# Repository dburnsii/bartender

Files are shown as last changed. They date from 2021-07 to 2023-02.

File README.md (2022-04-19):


# The Bartender

Product Video (https://youtu.be/YWqvJ5PAxSI)

The Bartender is an intelligent, robotic, drink-making machine. It's made to
display your bottles and pour you a cocktail just the way you like. The scale
ensures your ingredients are measured precisely, and the touchscreen interface
makes it easy to use. Each led in the light strip above the bottle deck can be
controlled individually, meaning they can highlight an empty bottle for you,
or they can put on a gentle light show to provide ambiance to a room. All told,
the Bartender is the perfect addition to any bar setup to make it quick, easy,
and fun to enjoy a casual drink, or to keep your guests glasses full.

## Contents
 - [About the Project](#About-the-Project)
 - [Getting Started](#Getting-Started)
 - [Hardware](#Hardware)
 - [Software](#Software)
 - [Contributing](#Contributing)
 - [Roadmap](#Roadmap)
 - [Contacts](#Contacts)

### About the Project
**The Bartender**'s design is made to integrate into a room first, and to easily
pour drinks second. The problem with many drink making machines is the need for
dedicated table space, which makes it feel like an appliance rather than a part
of your setup. With two drawers for storage, and knobs or handles on the front
side, **The Bartender** feels like a cabinet with some extra wizardry, and can
also hold things like Margarita Salt or tools like a stirrer.

[Demo Video](https://youtu.be/VJUhfgaUki0)

### Getting Started
The Bartender calls for equal parts hardware and software, so some woodworking
and soldering is required. Currently you'll have to buy the components and
assemble yourself, but if the project gains popularity, kits may become available.

### Hardware
As mentioned above, you'll need to do some woodworking to get the drinks
flowing. The cut list is available in the `hardware` directory, and the BOM
is available there as well. After purchasing and assembling the required
hardware, you can move on to getting the Raspberry Pi set up.

### Software
#### Build Requirements
 - [**Qemu User Static**](https://github.com/multiarch/qemu-user-static) - Multi-platform build support
  - [**Docker**](https://www.docker.com/) - Build environment

#### Development
- [**Kicad**](https://www.kicad.org/) - PCBs
- [**FreeCad**](https://www.freecadweb.org/) - 3D Models
- [**Platform.io**](https://platformio.org/) - For Arduino Companion

#### Runtime
 - [**Raspberry Pi OS**](https://www.raspberrypi.org/software/) - Operating System
 - [**React**](https://reactjs.org/) - Frontend
 - [**Python**](https://www.python.org/) - Backend Microservices

#### Installation
 1. Install [Raspberry Pi OS](https://www.raspberrypi.org/software/) on your Pi
 2. Add **The Bartender**'s official Debian repo to your `/etc/apt/sources.list` file:
   - `echo "deb https://storage.googleapis.com/bartender-repo bullseye main" | sudo tee -a /etc/apt/sources.list`
 3. Add **The Batender**'s secure GPG key for updates:
   - `wget -O - https://storage.googleapis.com/bartender-repo/bartender-repo.gpg.key | sudo apt-key add -`
 5. Reboot and grab a glass!

#### Updating
  Navigate to the "Settings" screen, and press "Upgrade". Reboot.

  The upgrade function is a very new feature, and may experience some problems.
  To troubleshoot, please file an issue here and run
  `sudo apt-get update && sudo apt-get -y upgrade` manually to get your system
  up to date.

### Contributing
This project is still in the early phases and the repo is subject
to changes and reorganization. Feel free to make suggestions and
submit a pull request for any desired features.

### Roadmap
The end goal for this project is to provide assembled units for anyone to use,
but getting there is a huge undertaking. With the help of contributors,
**The Bartender** can get there, but even if it doesn't, it's a fun project
to play with, and a great way to learn many different skills.

### License

See [LICENSE](LICENSE)

### Contacts
Desone Burns II - dburnsii@live.com - https://desone.dev

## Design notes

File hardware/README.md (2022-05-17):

# Hardware

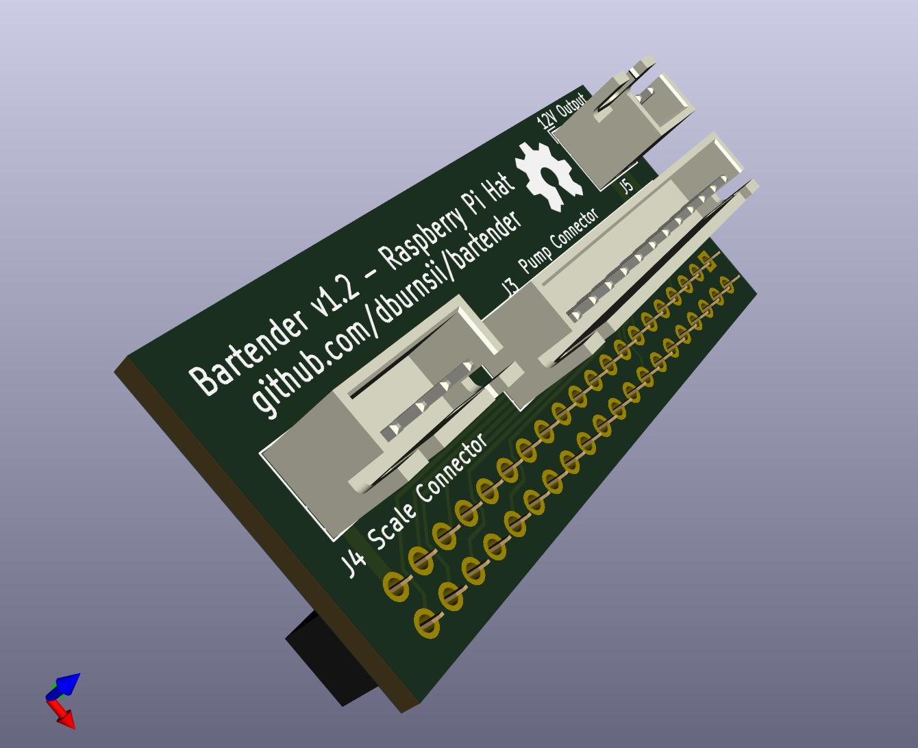
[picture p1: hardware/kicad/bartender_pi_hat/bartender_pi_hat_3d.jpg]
Pi Hat PCB


Here you'll find all the hardware you'll need to assemble your own **The Bartender**.
There are quite a few parts you'll need, and most of them can be purchased for very
cheap from eBay, however you'll likely end up with more parts than you'll need for
most things. As this project gains popularity, kits may become available to make
getting started a lot easier.

## Part List
The parts in the parts list were sourced due to their high availability. **The
Bartender** is a relatively advanced system, but it's made up of components that
are easy to get a hold of.

## Cut List

The list of cuts you'll need to make to the single 4'x8' sheet of plywood are
available in .csv format. My current favorite tool for this purpose is
[CutListOptimizer](https://www.cutlistoptimizer.com/). It isn't a FOSS tool,
but you should only need to use it once or twice, optimizing for the blade
you're using to cut the wood. The full 3D model of the bartender is available in
FreeCAD, with assembly instructions to come.

## Roadmap

The intention for this project is to combine and optimize these components
both for bringing down the price, and for ease of accessibility. I personally
(@dburnsii) am not a hardware engineer nor do I have a background in Hardware,
so I recognize that there is a lot of room for improvement in optimizing the
PCBs, cleaning up and optimizing the frame build, etc. My hope is that the
open-source community will band together and make this the drink-making robot
of the future!

### Milestones

#### Single Board Setup
**The Bartender** should have all connections come from the same PCB, rather than
using separate power supplies and a separate pump array board.

 - [ ] Run all 5v components from a 12v -> 5v buck converter (or other step-down)
 - [x] Run Neopixels (accent lighting above bottles) directly from the Pi
 - [ ] Affix the Pump-Controller board components to the Pi Hat

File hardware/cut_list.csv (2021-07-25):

Length | Width | Qty | Label | Enabled
48 | 24 | 1 | Frame Back | true
48 | 6 | 2 | Frame Top & Bottom | true
23 | 6 | 2 | Frame Left & Right | true
47 | 6 | 2 | Frame Shelves | true
6 | 4 | 2 | Drawer Barrier | true
16 | 4 | 2 | Drawer Faces | true
5 | 3.5 | 4 | Drawer Sides | true
15 | 3.5 | 2 | Drawer Rear | true
14 | 5 | 2 | Drawer Bottom | true
47 | 5.5 | 1 | Pump Door | true

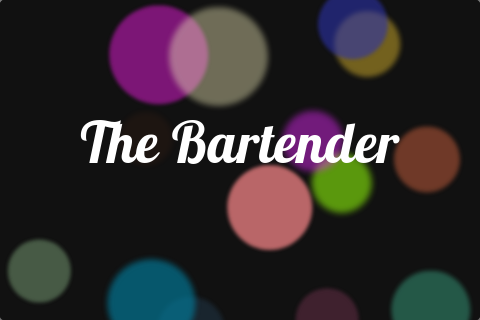
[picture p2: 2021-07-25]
screensaver.png

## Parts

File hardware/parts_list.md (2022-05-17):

# Parts List
Below is the list of parts that you'll need in order to build your own The Bartender!

### Custom PCBS
The Bartender has a few PCBs that make assembly and maintenance a lot easier:
 - [ ] [Pump Array](https://oshpark.com/shared_projects/H87zFAoN) - $26.80 (for 3, $8.93 each)
 - [ ] [Raspberry Pi Hat](https://oshpark.com/shared_projects/1Qw7b2lh) - $9.80 (for 3, $3.27 each)

 Total: $36.60 ($12.20 for a single set)

 All Prices are as listed from OshPark, and each order includes a minimum of 3 boards. The CAD files for these boards are provided, and you may be able to find them cheaper elsewhere.

### For the PCBs

#### Pump Array
 - [ ] 10x TIP-120 (~$6/10pcs)
 - [ ] 10x 1N4001 Diodes (~$3/10pcs)
 - [ ] 10x 1k Resistors (~$3/10pcs)
 - [ ] 11x 2-pin JST-XH Headers (~$5/50sets (includes cables))
 - [ ] 10x 2-pin JST-XH Cables (various lengths, for the pumps)
 - [ ] 1x 12-pin JST-XH Header ($5/20pcs)
 - [ ] 1x 12-pin JST-XH 20cm Cable ($9/5pcs)

#### Raspberry Pi Hat
 - [ ] 1x 12-pin JST-XH Connector (included above)
 - [ ] 1x 4-pin JST-XH Right-Angle Connector (~$5/10 sets)
 - [ ] 1x 3-pin JST-XH Connector (~$5/50sets)
 - [ ] 1x 2-pin JST-XH Connector (Optional, included above)
 - [ ] 1x 2x20-pin Female Header (~$2)

#### HX711 Module
 - [ ] 2x 4-Pin JST-XH Right-Angle Connector (included above)
 - [ ] 1x 10KG Load Cell (Often included with HX711 module)

Total: ~$43

### Off-The-Shelf
 - [ ] 1x Raspberry Pi 4 2GB ($35)
 - [ ] 1x 8GB MicroSD Card ($6)
 - [ ] 1x Waveshare 5" DSI Touchscreen ($45)
 - [ ] 1x HX711 Module (Shielded) ($2)
 - [ ] 1x 2M Addressable LED Strip ($15)
 - [ ] 1x 12v 1A Power Supply ($6)
 - [ ] 1x 5v 5A Power Supply (USB-C) ($7)
 - [ ] 1x Fused AC Inlet ($3)
 - [ ] 10x 365 DC Pump ($8)
 - [ ] 1x 1KG Roll of 3D Filament (Any Color) ($15)

Total: ~$142

### The Home Depot
 - [ ] 1x 4'x8'x1/2" Sheet MDF (~$37.00)
 - [ ] 2x Box Wood Screws (3/4" and 2") (~$5 + $10)
 - [ ] 3x Drawer Handles (~$5)
 - [ ] 4x Inset Cabinet Hinges ($8/pair)
 - [ ] 4x Double Roller Catch for Cabinet (~$1)
 - [ ] TBDx M4 Screws and nuts (~$10)
 - [ ] 1x 5m 1/4" ID 3/8" OD Vinyl Tubing (~$10)
 - [ ] 1x 1m 3/8" ID 1/2" OD Vinyl Tubing (~$4)

Total: ~$101

### Tools
 - [ ] Circular or Table Saw
 - [ ] Soldering Iron
 - [ ] Drill
 - [ ] Spade Drill Bit Set

Grand Total: ~$298.20

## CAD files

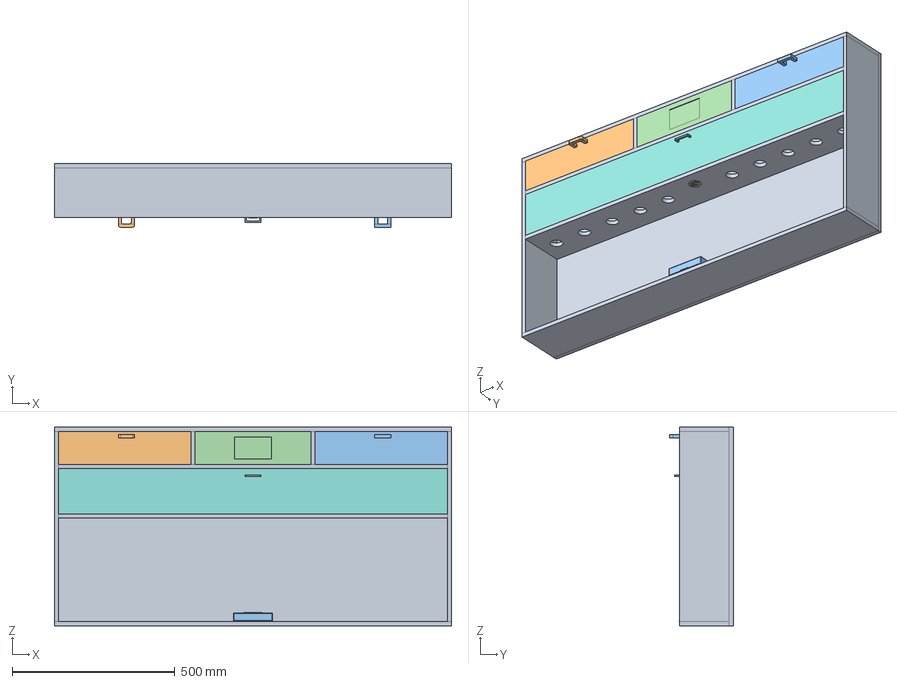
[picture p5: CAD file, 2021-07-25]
hardware/freecad/BartenderAssembly.FCStd
1219.2 x 195.1 x 609.6 mm
FullFrame
SpoutGuide
ScaleBody
ScalePlate
ScaleBracket
LoadCell
ScaleBaseTray
PumpDoor
LCD
SpareDrawerLeft
SpareDrawerRight
LCD Holder

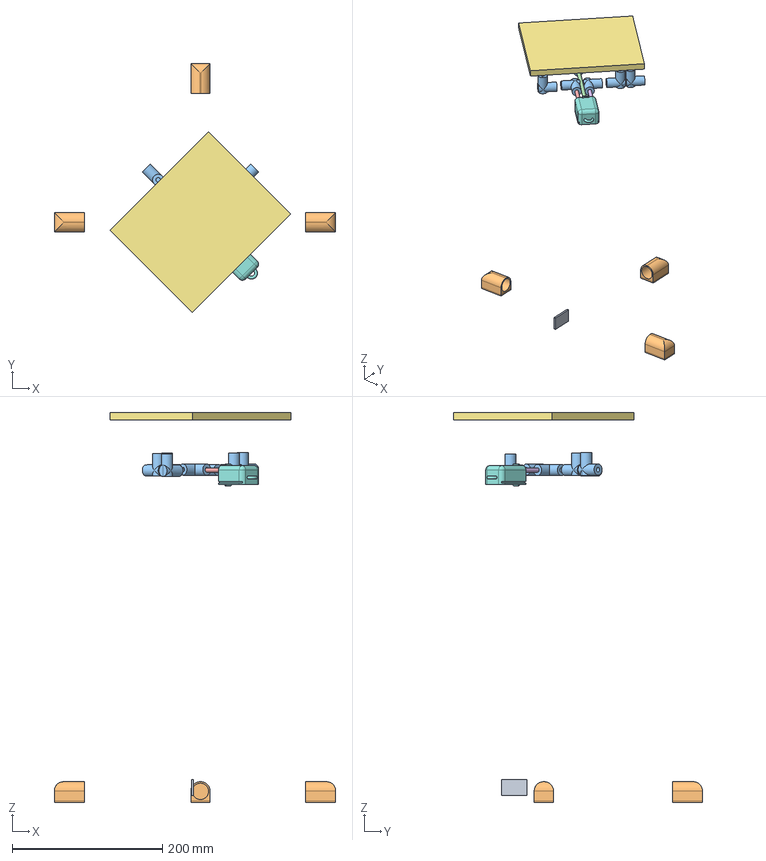
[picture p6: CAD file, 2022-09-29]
hardware/freecad/Mini/BartenderMini.FCStd
374.5 x 331.2 x 518.9 mm
ScalePCB
Foot South x 3
Tubing Elbow 001 x 7
Tubing 001
Tubing 002
Tubing 003
Lid
Spout

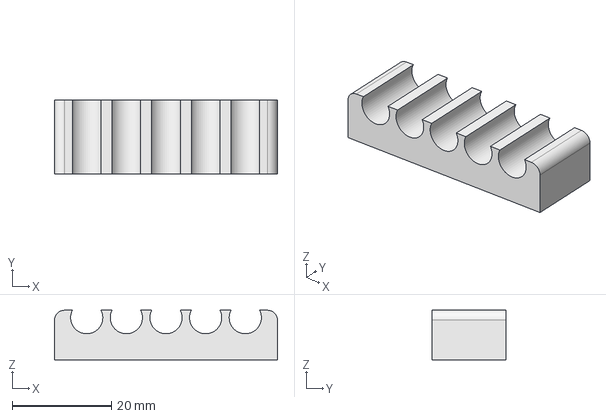
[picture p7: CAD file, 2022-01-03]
hardware/freecad/TubingGuide.FCStd
45.0 x 15.0 x 10.0 mm

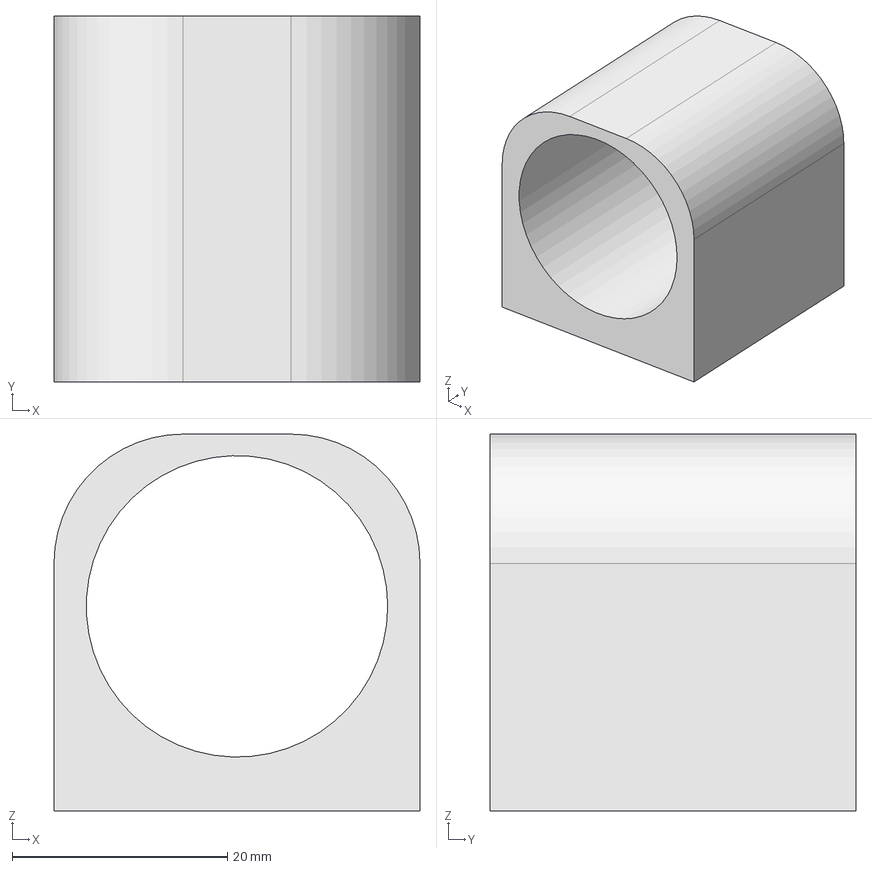
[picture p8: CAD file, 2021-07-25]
hardware/freecad/PumpHolder.FCStd
34.0 x 34.0 x 35.0 mm

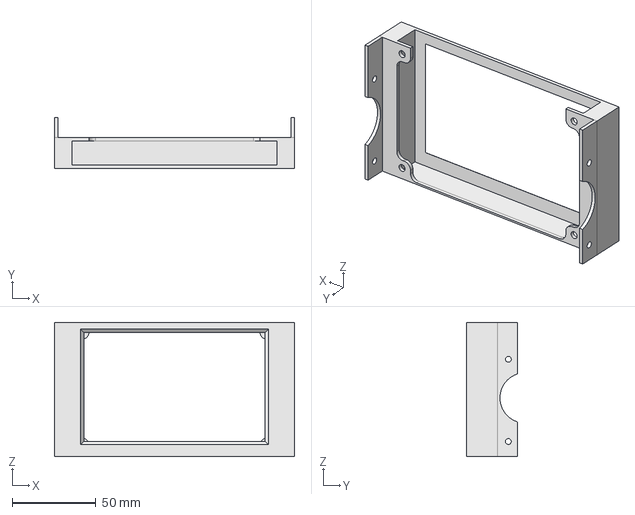
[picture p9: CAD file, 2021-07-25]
hardware/freecad/ScreenMountv2.FCStd
143.0 x 30.5 x 80.0 mm

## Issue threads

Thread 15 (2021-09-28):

Add manual pour mode

dburnsii, 2021-09-28:

dburnsii, 2021-09-28:
Certain ingredients are currently not compatible with the bartender (i.e. carbonated liquids). There should be a way to pour these ingredients into the glass manually, using the LEDs to indicate to the user how much to pour (still utilizing the scale).

Closed 2022-01-03.

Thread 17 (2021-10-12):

Add calibration configuration

dburnsii, 2021-10-12:
HX711 modules tend to be subject to some temperature drift as well as some sensitivity drift. Add a page to the interface to calibrate with a known amount of liquid or weight.

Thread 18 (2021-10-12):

Add upgrade button

dburnsii, 2021-10-12:
Now that the database is transferred to sqlalchemy and migrations are possible, create an `upgrade.sh` script to check for system upgrades (currently via the git repo), to be launched by the system service. Subsequently rebuild the frontend and run any migrations, then reboot.

Closed 2022-04-13.

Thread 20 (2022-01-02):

Add cleaning mode

dburnsii, 2022-01-02:
One of the menus available should be a cleaning mode. The pumps should add in "last loaded" and "last cleaned" columns to the database, for letting users know in the future when they should clean a pump. The cleaning mode should be simple: activate it for a given pump with the water loaded, run some amount of water through (maybe a couple cleaning mode levels), and do some pulses to free anything that may be stuck.

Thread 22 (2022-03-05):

Eliminate the companion chip

dburnsii, 2022-03-05:
LED strip should be driven directly by RPi

dburnsii, 2022-03-10:
Driving the LED strip directly from the RPi has been validated, but will require some rework to the led_server, as well as an update to the PCB HAT.

dburnsii, 2022-03-10:
Depends on #29

Closed 2022-09-25.

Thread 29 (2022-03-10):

Integrate Motor driver and HAT

dburnsii, 2022-03-10:
The motors for the bartender can be driven by an SMD transistor. Rework the PCB to integrate the motor driver to use SMD components, and also include a port for the LED strip in the rework.

Closed 2023-01-15.

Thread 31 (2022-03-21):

Firefox over Chromium or other browsers

dburnsii, 2022-03-21:
This issue is just for record keeping purposes.

The motivation for choosing Firefox over Chromium for this project is that Chromium supports a minimum browser height of 500 pixels, where the screen in use is only 480. The html element could be modified to account for this, but leads to a bunch of exceptions in the case to make it work, which will make it harder to get this working on external devices (phone browsers for instance)

Closed 2022-03-21.

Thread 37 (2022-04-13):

Rework manual pour screen

dburnsii, 2022-04-13:
Instead of cramming all of the bottle actions into a small space, perhaps make the manual pour screen more of a menu, where the user selects the desired bottle, and then a modal pops up with more options. This modal could have more than just a pour button, it could also have options for measured pours.

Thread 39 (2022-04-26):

Reduce SD Card Writes

dburnsii, 2022-04-26:
By default, Raspberry Pi OS does lots of reads and writes to the SD card. Since the lifespan of these cards is relatively short, add settings to reduce the number of reads and writes as much as possible.

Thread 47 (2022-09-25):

Convert LEDs to I2C

dburnsii, 2022-09-25:
With looking at multiple boards, and considering some of the issues seen with custom protocols regarding timing, all devices that communicate with the main board should be communicating with I2C.

For the LEDs, this will likely mean creating a custom firmware on an MCU, likely an Arduino. This will differ from the old design in that it will use protocol closer to how the pixels actually work, and it will be over I2C instead of UART over USB.

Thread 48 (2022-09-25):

Convert scale to I2C

dburnsii, 2022-09-25:
With looking at multiple boards, and considering some of the issues seen with custom protocols regarding timing, all devices that communicate with the main board should be communicating with I2C.

The scale will just need a 24-bit ADC to replace the Hx711. This will likely provide more accuracy anyway.

dburnsii, 2022-10-20:
There are a few good options for this chip, but one that has some good support and is widely available is the following:

https://www.digikey.com/en/products/detail/nuvoton-technology-corporation/NAU7802SGI/2769782

dburnsii, 2023-01-15:
Adafruit has a good option for this, that won't require a custom board:

https://www.adafruit.com/product/4538  - Adafruit NAU7802 24-Bit ADC - STEMMA QT / Qwiic

dburnsii, 2023-02-04:
Code has been written to read from an NAU7802, and the OTS board from Adafruit works great. Only thing left is to add some setup and add some qwiic connectors to the Pi hat, that'll be covered in another ticket.

Closed 2023-02-04.

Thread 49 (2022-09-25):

Convert motor board to I2C

dburnsii, 2022-09-25:
With looking at multiple boards, and considering some of the issues seen with custom protocols regarding timing, all devices that communicate with the main board should be communicating with I2C.

The problem with the motor board is that it requires 10 discreet GPIO outputs, rework the board to use the MCP23017

dburnsii, 2022-10-20:
MCP23017 chips seem to be in low supply currently. The following may be a good alternative:

https://www.digikey.com/en/products/detail/nxp-usa-inc/PCA9555APW-118/3677025

dburnsii, 2023-01-26:
New board wel PCAL6416A tested and working well, adding and testing new module to drive it and setting a place to select it in configuration.

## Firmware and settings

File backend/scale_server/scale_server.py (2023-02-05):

#!/usr/bin/env python3

import socketio
import time
import sys
import requests
from simulated_scale import Simulator

import gc
last_weight = time.time()


sio = socketio.Client()
connected = False
present = False
simulation = True
simulated_pour_status = False
weight = 0
measures = [0, 0, 0]
# TODO: Make this user selectable
# calibration = 222.23
calibration = 10000
cup_threshold = 30
bad_reads = 0
adc = None
adc_module = "simulation"  # One of: "hx711", "nau7802", or "simulation"
manual_target = 0
manual_start = 0
config_url = "http://localhost:5000/config/"


def cleanup():
    global adc
    global adc_module
    print("Cleanup")
    if not simulation:
        if adc_module == "hx711":
            GPIO.cleanup()
        elif adc_module == "nau7802":
            adc.cleanup()
    sio.disconnect()
    gc.collect()
    sys.exit()


def variance():
    return max(measures) - min(measures)


def get_config(key):
    r = requests.get(config_url + key)
    if r.ok:
        print(r.text)
        return r.text.strip().replace("\"", "")
    else:
        print("Error getting config: '{}'".format(key))
        return None


def set_config(key, value):
    r = requests.put(config_url + key, value)
    if r.ok:
        print("Successfully updated: {}".format(key))
    else:
        print("Failed to update config: {}".format(key))


@sio.event
def cup_presence_request(data):
    global present
    print("Broadcasting presence '{}'".format(present))
    sys.stdout.flush()
    sio.emit('cup_presence', {'present': present})


@sio.event
def manual_pour_init(data):
    global present
    global weight
    global manual_target
    global manual_start

    print("Received manual pour request: {}".format(data))
    # TODO: Leave this out until we can stabilize the cup detection. Might
    #       also be good to leave out for cleaning.
    # if not present:
    #    return
    manual_target = data['quantity']
    manual_start = weight


@sio.event
def weight_request():
    global weight
    sio.emit('weight', {'weight': weight})


@sio.event
def simulation(data):
    global simulation
    global adc
    global adc_module
    simulation = data['status']
    print(simulation)

    adc_module = get_config("scale_controller")

    print("Initializing hardware")
    if adc_module == "simulation":
        adc = Simulator()
    elif adc_module == "hx711":
        global GPIO
        global HX711
        import RPi.GPIO as GPIO
        from hx711 import HX711
        print("Initializing HX711")
        adc = HX711(6, 5)
        adc.set_reference_unit(1)
        adc.reset()
        adc.tare()
    elif adc_module == "nau7802":
        print("Initializing NAU7802")
        global NAU7802
        from nau7802 import NAU7802
        adc = NAU7802(gain=128)
    else:
        print("No valid module selected.")
        adc = Simulator()
    print("Scale ready!")


@sio.event
def simulated_pour(data):
    print("Detected simulated pour")
    global simulated_pour_status
    simulated_pour_status = data['status']


@sio.event
def tare_scale(data):
    print("Zeroing scale")
    global adc
    global present
    adc.reset()
    adc.tare()
    present = False
    cup_presence_request("")


@sio.event
def calibrate_scale(data):
    global adc
    global calibration
    global simulation
    print("Calibrate")
    if "weight" not in data:
        print("Missing known weight")
        return
    known_weight = data["weight"]
    if simulation:
        current_weight = 100
    else:
        current_weight = adc.get_weight(10)
    calibration = known_weight / current_weight
    print("New calibration value: {}".format(calibration))
    set_config("scale_calibration", str(calibration))


@sio.event
def disconnect():
    print("Disconnected...")
    sys.stdout.flush()
    global connected
    connected = False


@sio.event
def connect():
    print("Connected!")
    sys.stdout.flush()
    sio.emit("register", {"name": "scale"})

    global connected
    connected = True


if __name__ == "__main__":
    sio.connect('http://localhost:8080')

    calibration = int(get_config("scale_calibration"))
    if calibration is None:
        calibration = 100

    while 1:
        try:
            if not simulation and adc:
                starttime = time.time()
                val = adc.get_weight(3)
                weight = val / calibration

                # If the read from the scale happens in less than 3ms, this is
                # usually because we're not actually able to communicate
                # with the hx711 module. Report this to the rest of the system.
                readtime = (time.time() - starttime)*1000
                print("{:.1f}g - {}ms".format(weight, readtime))
                if (readtime < 3):
                    # Try to only notify the rest of the system every once in
                    # a while
                    print("Error reading scale.")
                    bad_reads += 1
                    if (bad_reads == 10):
                        bad_reads += 1
                        sio.emit("error", {"title": "Scale Not Responding",
                                 "text": ("Currently unable to get a read "
                                          "from the scale. Please make sure "
                                          "it's properly connected.")})
                    time.sleep(1)
                    continue
                else:
                    if (bad_reads > 0):
                        sio.emit("clear_error", {"title":
                                                 "Scale Not Responding"})
                    bad_reads = 0

                measures.append(weight)
                measures.pop(0)
                if (weight > cup_threshold and variance() < 5 and not present):
                    print("Cup detected")
                    present = True
                    cup_presence_request()
                    adc.tare()
                    continue
                elif (weight < (cup_threshold * -0.5) and
                      variance() < 5 and
                      present):
                    print("Cup removed")
                    present = False
                    cup_presence_request()
                    adc.tare()
                elif (manual_target > 0):
                    manual_percentage = (weight - manual_start) / manual_target
                    print("Manual percentage: {}".format(manual_percentage))
                    if (manual_percentage >= 1.0):
                        print("Manual pour complete!")
                        manual_target = 0
                        sio.emit('manual_pour_status', {
                                'percentage': manual_percentage,
                                'complete': True})
                    else:
                        sio.emit('manual_pour_status', {
                                'percentage': manual_percentage,
                                'complete': False})
                weight_request()
                time.sleep(0.05)
            elif connected:
                if simulated_pour_status:
                    if not present:
                        present = True
                        cup_presence_request()
                    weight += 2
                    if manual_target > 0:
                        manual_percentage = \
                            (weight - manual_start) / manual_target
                        print("Manual percentage: {}"
                              .format(manual_percentage))
                        if (manual_percentage >= 1.0):
                            print("Manual pour complete!")
                            manual_target = 0
                            sio.emit('manual_pour_status', {
                                'percentage': manual_percentage,
                                'complete': True})
                        else:
                            sio.emit('manual_pour_status', {
                                'percentage': manual_percentage,
                                'complete': False})
                else:
                    if present:
                        present = False
                        weight = 0
                        cup_presence_request()
                weight_request()
                time.sleep(0.1)
            else:
                print("Not connected...")
                # sio.connect('http://localhost:8080')
                time.sleep(1)

        except (KeyboardInterrupt, SystemExit):
            cleanup()

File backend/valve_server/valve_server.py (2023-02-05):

#!/usr/bin/python3

import utils
import time
import sys
import atexit
import socketio
import requests


controller = None
controller_type = "simulation"  # One of: simulation, gpio, mcp23017
pour_target = 0
pour_total = 0
pour_queue = []
scale_heartbeat = time.time()
scale_cache = []
scale_cache_size = 20
cup_presence_status = False
scale_failure_threshold = 5
manual_override = False
manual_pour_active = False

sio = socketio.Client()


@atexit.register
def cleanup():
    sio.disconnect()
    if not simulation:
        for pin in pins:
            gpio.setup(pin, gpio.OUT)
            gpio.output(pin, gpio.LOW)
        gpio.cleanup()


def get_config(key):
    r = requests.get(config_url + key)
    if r.ok:
        print(r.text)
        return r.text.strip().replace("\"", "")
    else:
        print("Error getting config: '{}'".format(key))
        return None


@sio.event
def activate_valve(data):
    global cup_presence_status
    global controller
    global manual_override

    print("Activating Valve: {}".format(data['pin']))
    if cup_presence_status or manual_override:
        controller.activate(int(data['pin']))


@sio.event
def deactivate_valve(data):
    print("Deactivating Valve: {}".format(data['pin']))
    # As of right now, we can only allow one valve to operate
    # at a time, due to the scale constraints. If this is
    # overcome, this may resume deactivating single valves,
    # but until then, it doesn't hurt to make sure all valves
    # are turned off.
    deactivate_valves()


@sio.event
def deactivate_valves(data=None):
    print("Shutting off all valves.")
    for pin in range(controller.count):
        controller.deactivate(pin)


@sio.event
def drink_pour(data):
    global pour_queue
    global pour_target
    global simulation
    global pour_total
    global scale_cache
    global cup_presence_status
    if (len(pour_queue)):
        print("Uh... we're  little busy...")
        sio.emit("error", {"title": "Pour in progress",
                           "text": "A drink is currently being poured. please"
                                    "wait until the drink is complete before "
                                    "beginning another pour."})
        return
    if not simulation and not cup_presence_status:
        print("Cup presence not detected. Aborting pour.")
        sio.emit("error", {"title": "Missing Cup",
                           "text": "No cup detected on the scale. Please "
                                   "place a cup on the scale before pouring a "
                                   "drink."})
        return

    print("Pouring you a drank, oh-woah-we-woah")
    valves = utils.grab_valves()
    drink = utils.grab_drink(data["id"])
    pour_queue = []
    pour_total = 0
    for ingredient in drink["ingredients"]:
        if not utils.ing_pourable(ingredient):
            print("Skipping non-pourable ingredient: {}".
                  format(ingredient["ingredient"]))
        elif (utils.ing_available(ingredient, valves)):
            print("Found a loaded ingredient")
        elif (not ingredient["required"]):
            print("Skipping a non-required ingredient")
        else:
            print("{} not in {}".format(ingredient["ingredient"], valves))
            sio.emit("error",
                     {"title": "Missing Ingredients",
                      "text": "Missing ingredient required "
                              "to pour {}: {}"
                      .format(drink["name"], ingredient["ingredient"])})
            return
    print("Ready to pour!")
    (pour_queue, pour_total) = utils.create_drink_queue(
        drink["ingredients"], valves)
    first_ingredient = pour_queue.pop(0)
    pour_target = scale_cache[-1] + first_ingredient["quantity"]
    print("Pour target: {}".format(pour_target))
    sio.emit("drink_pour_active", {"status": True})
    controller.activate(first_ingredient["pin"])
    # Add a rouge value to trick the variance algorithm into thinking the pour
    # has started
    if (len(scale_cache) > 100):
        scale_cache.pop(0)
    scale_cache.append(-100)


@sio.event
def abort_pour(data):
    global pour_target
    global pour_queue
    global manual_pour_active
    deactivate_valves()
    pour_target = 0
    pour_queue = []
    manual_pour_active = False
    sio.emit("drink_pour_active", {"status": False, "progress": 0})
    sio.emit("manual_pour_status", {"complete": True, "progress": 0})


@sio.event
def manual_pour_status(data):
    global manual_pour_active
    if data['complete']:
        manual_pour_active = False


@sio.event
def weight(data):
    global scale_cache
    global scale_heartbeat
    global pour_queue
    global pour_target
    global pour_total
    global scale_cache_size
    global manual_pour_active

    # Cache the recent scale values for no-progress detection
    scale_cache.append(data["weight"])
    if (len(scale_cache) > scale_cache_size):
        scale_cache.pop(0)
    scale_heartbeat = time.time()

    # Check if we finished pouring our last ingredient
    if pour_target > 0:
        if (manual_pour_active is False and
           utils.variance(scale_cache) < scale_failure_threshold):
            print("Minimum variance detected on scale. Aborting pour. "
                  "Check to make sure bottle is connected and flowing.")
            abort_pour("")
            return
        if scale_cache[-1] >= pour_target:
            print("Ingredient target reached!")
            deactivate_valves()
            pour_target = 0
            if (len(pour_queue)):
                print(pour_queue)
                ingredient = pour_queue.pop(0)
                pour_target = scale_cache[-1] + ingredient["quantity"]
                print("Pour target: {}".format(pour_target))
                sio.emit("drink_pour_active", {"status": True})
                if ingredient["pin"] is None:
                    print("Kick off manual pour!")
                    manual_pour_active = True
                    sio.emit("manual_pour_init", {
                        "name": ingredient["name"],
                        "quantity": ingredient["quantity"]})
                    sio.emit("simulated_pour", {"status": True})
                else:
                    controller.activate(ingredient["pin"])
            else:
                print("Finished pouring drink!")
                sio.emit("drink_pour_active", {"status": False, "progress": 0})
        else:
            remaining_total = utils.remaining_in_queue(pour_queue)
            remaining_current = pour_target - scale_cache[-1]
            progress = (pour_total - (remaining_current +
                        remaining_total)) / (pour_total) * 100
            sio.emit("drink_pour_active", {
                     "status": True, "progress": progress})


@sio.event
def cup_presence(data):
    global cup_presence_status
    cup_presence_status = data["present"]
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

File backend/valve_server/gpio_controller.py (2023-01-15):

import RPi.GPIO as gpio
from controller import Controller


class GpioController(Controller):
    def __init__(self):
        self.pins = [21, 26, 20, 19, 16, 12, 22, 23, 27, 4]
        self.count = len(self.pins)
        gpio.setmode(gpio.BCM)
        for pin in self.pins:
            gpio.setup(pin, gpio.OUT)
            gpio.output(pin, gpio.LOW)

    def activate(self, index):
        gpio.output(self.pins[index], gpio.HIGH)

    def deactivate(self, index):
        gpio.output(self.pins[index], gpio.LOW)

    def cleanup(self):
        for pin in self.pins:
            gpio.output(pin, gpio.LOW)

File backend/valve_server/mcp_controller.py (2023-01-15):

import board
import busio
from digitalio import Direction
from adafruit_mcp230xx.mcp23008 import MCP23017

from controller import Controller


class GpioController(Controller):
    def __init__(self, count=10):
        self.pins = [8, 9, 10, 11, 12, 13, 14, 15, 0, 1, 2, 3, 4, 5, 6, 7]
        self.count = count
        i2c = busio.I2C(board.SCL, board.SDA)
        self.mcp = MCP23017(i2c)

        for i in range(self.count):
            pin = mcp.get_pin(self.pins[i])
            pin.direction = Direction.OUTPUT
            pin.value = False

    def activate(self, index):
        if index >= count or index < 0:
            print("Invalid pin: {}".format(index))
            return
        pin = self.mcp.get_pin(self.pins[index])
        pin.value = True

    def deactivate(self, index):
        if index >= count or index < 0:
            print("Invalid pin: {}".format(index))
            return
        pin = self.mcp.get_pin(self.pins[index])
        pin.value = True

    def cleanup(self):
        for pin_index in self.pins:
            pin = self.mcp.get_pin(pin_index)
            pin.value = False

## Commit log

2021-07-25 Initial Release
    [BartenderAssembly.FCStd, PumpHolder.FCStd, ScreenMountv2.FCStd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]
2021-08-12 Fix pin order for new rpi hat
    [valve_server.py]
2021-08-31 Fix linter issues and enable linter checks
    [hx711.py, led_server.py, scale_server.py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]
2021-10-07 Update led server to display progress
2022-01-03 Added tubing guide CAD model
    [TubingGuide.FCStd]
2022-02-07 Initial debian package
    [bartenderconfig.txt]
2022-03-17 Lots of updates to add an upgrade button to the UI
2022-04-06 Changes for RPi LED Controller
    [BartenderMini.FCStd, bartender_pi_hat.kicad_pcb, bartender_pi_hat.kicad_sch]
2022-04-09 Added lock screen switch, and activates on screensaver
2022-04-19 Update GND for all RPi Pins
    [bartender_pi_hat.kicad_pcb, bartender_pi_hat.kicad_sch]
2022-04-22 Run LEDs directly
2022-04-24 Convert led pixels to class, and set up system to use LEDs directly
2022-05-04 Updates for using hardware LEDs
2022-05-05 Update progress for leds
2022-05-17 Updates for installation
    [bartenderconfig.txt]
2022-06-08 Style changes for led server
2022-09-29 Got wifi up and running, started work on the Mini
    [BartenderMini.FCStd, bartender_pump_array.kicad_pcb, bartender_pump_array.kicad_sch]
2022-11-22 Updates for NAU7802 ADC and NetworkManager
2023-01-15 Updates for build, scale setup, new copy of pump board, etc
    [bartender_pump_array.kicad_pcb, bartender_pump_array.kicad_sch]
2023-02-05 Update to pull scale and valve from config, update boards
    [bartender_pi_hat.kicad_pcb, bartender_pi_hat.kicad_sch, bartender_pump_array.kicad_pcb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]
